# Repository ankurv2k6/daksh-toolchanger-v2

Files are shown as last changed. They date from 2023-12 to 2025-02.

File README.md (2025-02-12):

# DAKSH V2 3D Printed Tool Changer - Open Beta

DAKSH V2 3D Printed Tool Changer is a fully 3D printed mechanical tool changer compatible with different CoreXY platforms like the Voron Trident, 1.8, 2.4  and RatRig VCore 3. The servo less mechanical locking mechanism is inspired by the Prusa XL - but is fully 3d printed with metal inserts in the critical areas for rigidity and reliability.

Salient Features: 

  * Fully Mechanical Tool Changer
  * Ultra Fast tool changing time of under 4 seconds
  * Fully 3d Printed and assembled using off the shelf components - no machined parts required
  * Intelligent Error State Detection and Recovery minimizing failed prints
  * Intelligent Tool Heating Management for faster and efficient prints
  * Automatic XYZ calibration across the different tools
  * Capable of High accelerations and print speeds
  * Minimal loss in build space with the tool changer addition
  * Integrated nozzle ooze blockers for clean prints with minimal waste
  * Status LEDs on each toolhead for accurate visual state diagnosis
  * Custom Klipper configuration, modules and macros for an integrated software package
  * Stiff Wire Looms and recoil management - wire looms are entirely contained within the printer frame itself.
  * Fully Enclosed Design in the same design ethos as the original Voron Trident design - giving it the ability to print high temp materials like ABS, PA6-CF and PC-CF etc which require enclosed chambers.

The design is open source and can be used freely for non commercial purposes. 

Do join the discord group at the link below and subscribe to the Youtube channel for more updates and interesting projects like this.

* [Github](https://github.com/ankurv2k6/wp-daksh-toolchanger-v2)
* [Youtube](https://www.youtube.com/channel/UCr8K1tva2CaEhyqNyaEjq_w)
* [Daksh V2 Discord](https://discord.gg/wJqUzYxYXH)
* [BOM](https://github.com/ankurv2k6/daksh-toolchanger-v2/tree/main/BOM) Create a copy of this [Google sheet](https://docs.google.com/spreadsheets/d/11UvXF6FBCVRHxjejWgnOjJhMhHBDZpzY7ktGSjUUAWM/edit?usp=sharing) for a checklist

Build Log and Demo videos 
* COMING SOON....

**5 Colour PLA Print - 0.6mm Nozzle / 0.25 Layer Height / 23 Hours / 2000 Tool Changes - TimeLapse**
Vase Print (https://www.youtube.com/watch?v=5WeLoIn3UTw)
  
**5 Colour PLA Print - 0.6mm Nozzle / 0.25 Layer Height / 23 Hours / 2000 Tool Changes**
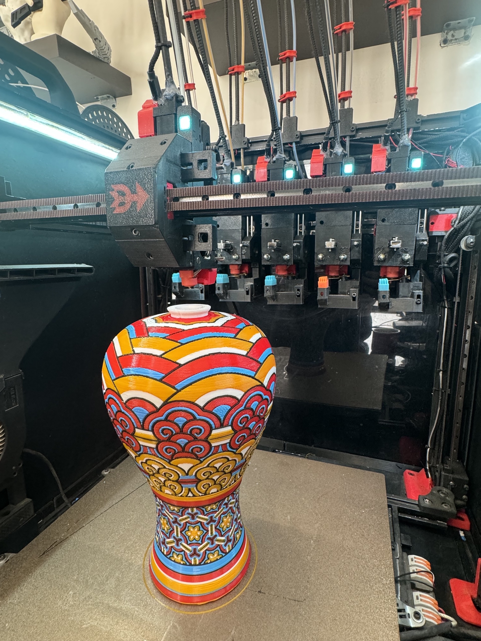
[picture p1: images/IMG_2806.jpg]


**5 Colour PLA Print - 0.6mm Nozzle / 0.25 Layer Height / 3 Hours / 300 Tool Changes**  
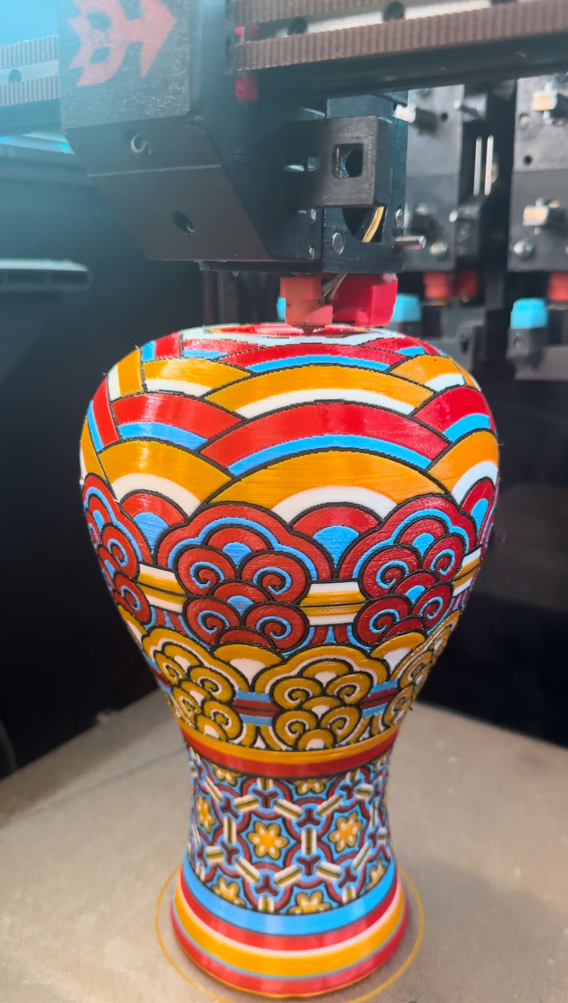
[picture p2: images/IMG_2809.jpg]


**TPU + PLA Print - 0.6mm Nozzle / 0.25 Layer Height / 23 Hours / 2000 Tool Changes**  
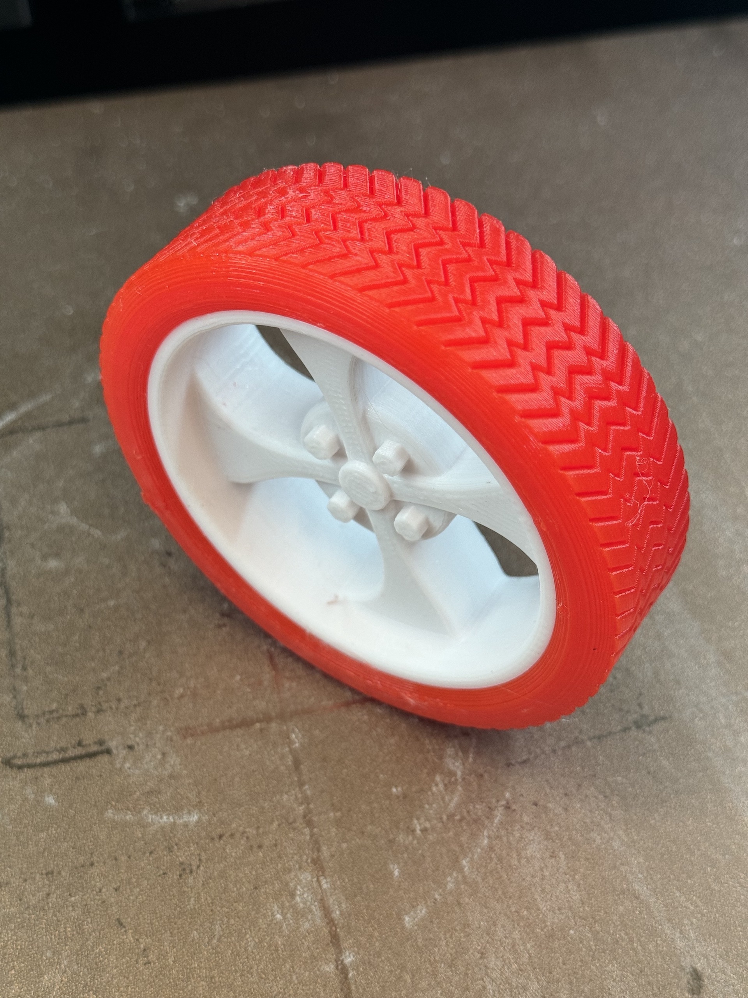
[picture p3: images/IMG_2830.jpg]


**TPU + PLA Print - 0.6mm Nozzle / 0.25 Layer Height / 8 Hours / 900 Tool Changes**  
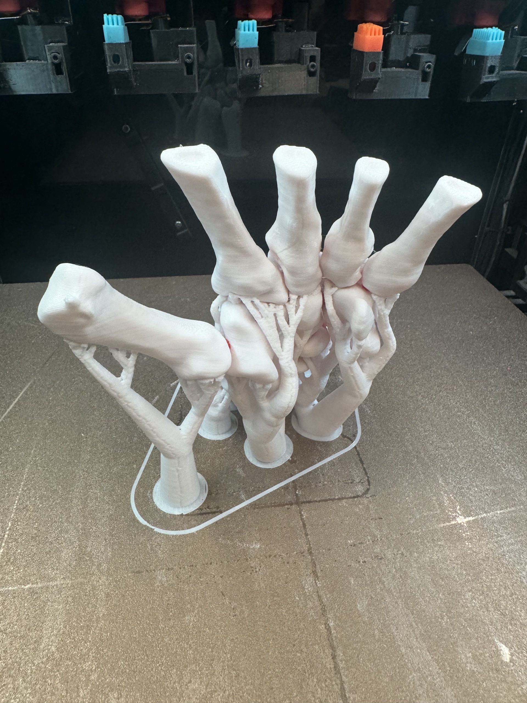
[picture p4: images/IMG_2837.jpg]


**5 Colour PLA + PETG Support print - 0.6mm Nozzle / 0.25 Layer Height / 3 Hours / 600 Tool Changes**  
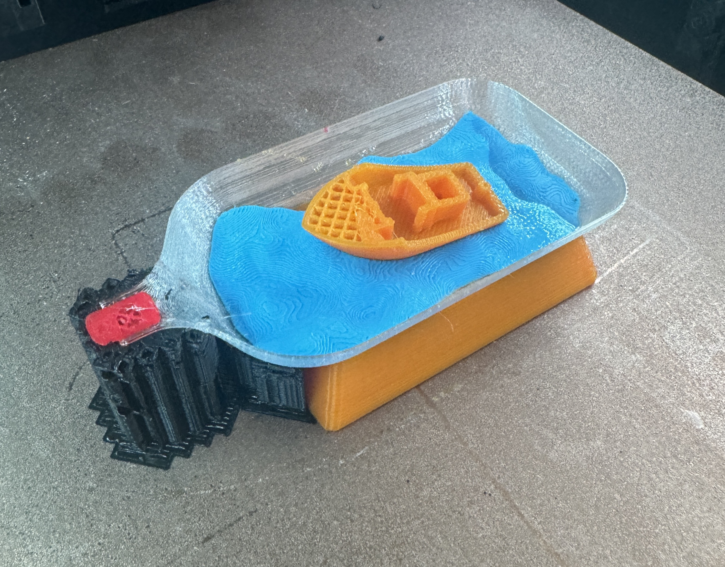
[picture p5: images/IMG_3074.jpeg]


Build Images
* COMING SOON....

Attributions - This project uses elements from a bunch of different projects by awesome people out there - I will be including a list of credits soon. My apologies for not doing that at the very onset due to paucity of time.

* [Quad Belted Z in based on the excellent work by genevamotion & thiagolocatelli](https://github.com/3DPrintingMods/VoronTrident-BeltedZ)

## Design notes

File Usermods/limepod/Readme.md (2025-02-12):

## limepod's mods

This is an overhaul of many parts, and none are made to be compatible with the original files.

* The XY Joints are modified to re-use the CNC top half from siboor
* The front idlers are remade to include tensioning, and moved forward to leave more space for the Y axis
* The A/B motor mounts are remade to be much bulkier, and the dock bar is now supported by aluminum brackets
* The carriage is modified to print in multiple parts, and various other changes to ease maintenance
* The toolheads have a number of changes, including the acorn nuts being shifted slightly, which makes them incompatible with the stock carriage

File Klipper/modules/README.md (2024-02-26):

Attributions

* Klipper Toolchanger - https://github.com/TypQxQ/Klipper_ToolChanger
* Tool Probe & Rounded Path - https://github.com/viesturz/klipper-toolchanger/
* Nozzle Align - https://github.com/viesturz/NozzleAlign
* ATC Switch - https://github.com/ben5459/Klipper_ToolChanger
* LED Effects - https://github.com/julianschill/klipper-led_effect

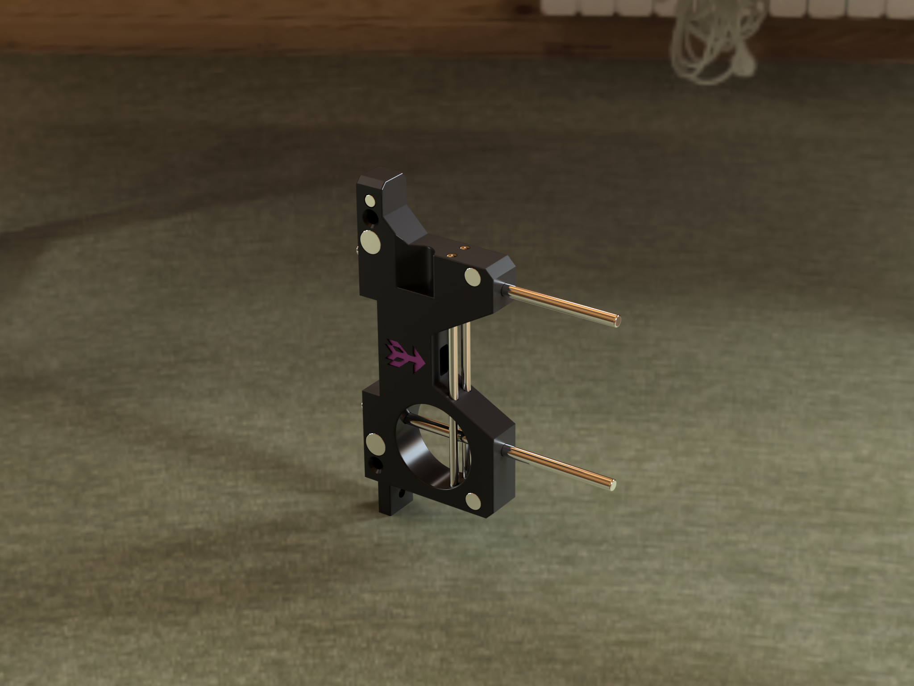
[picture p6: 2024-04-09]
Usermods/3dfiyMyLife/Sherpa-Mini-Orbiter-Extruder/Daksh Dock Mod.png

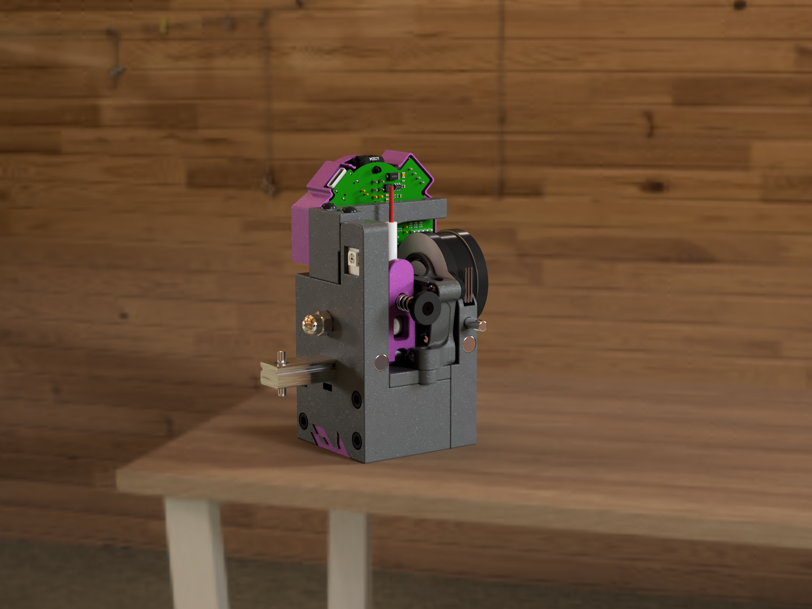
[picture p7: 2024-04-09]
Usermods/3dfiyMyLife/Sherpa-Mini-Orbiter-Extruder/Daksh Sherpa Mini.png

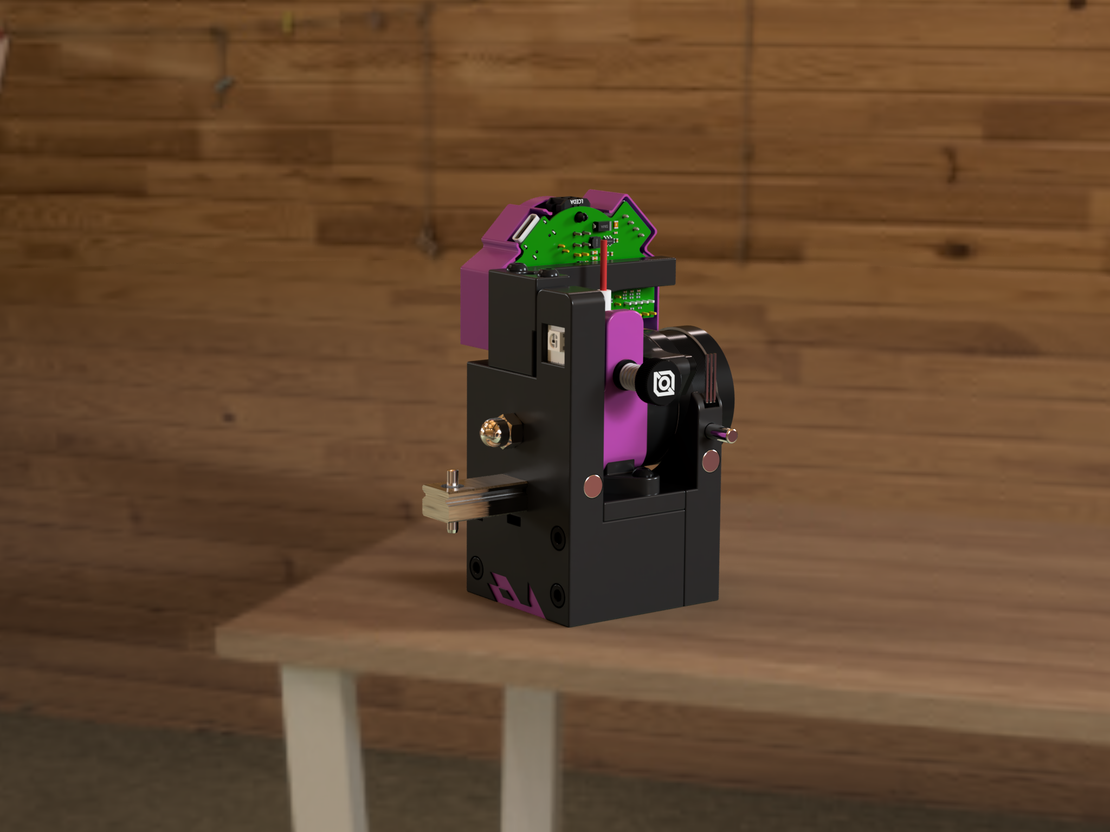
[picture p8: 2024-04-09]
Usermods/3dfiyMyLife/Sherpa-Mini-Orbiter-Extruder/Daksh Orbiter.png

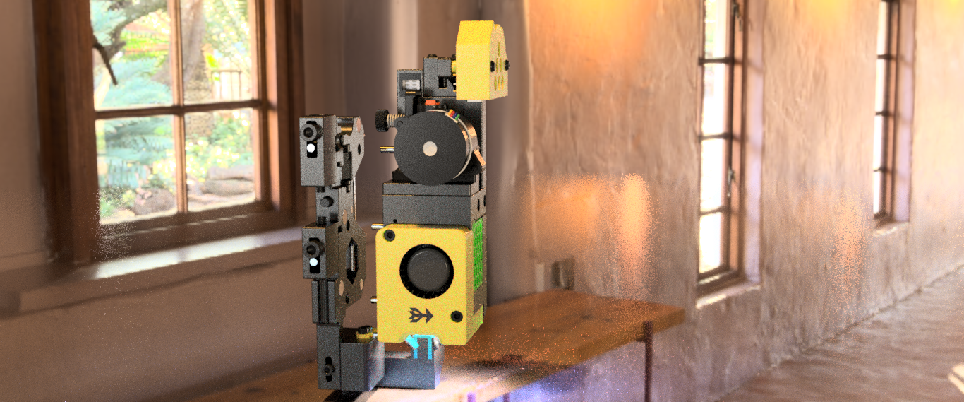
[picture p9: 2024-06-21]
CAD/V2ool/Rear_Docking/Daksh V2ool.png

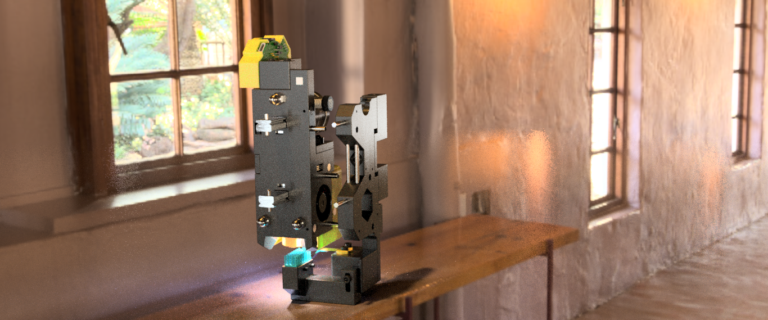
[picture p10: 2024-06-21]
CAD/V2ool/Rear_Docking/Daksh V2ool (1).png

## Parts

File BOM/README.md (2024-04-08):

Please refer to the [Google Sheets](https://docs.google.com/spreadsheets/d/11UvXF6FBCVRHxjejWgnOjJhMhHBDZpzY7ktGSjUUAWM/edit?usp=sharing) for the latest list

Create a copy of [Google Sheets](https://docs.google.com/spreadsheets/d/11UvXF6FBCVRHxjejWgnOjJhMhHBDZpzY7ktGSjUUAWM/edit?usp=sharing) to act as your own checklist 

| Item | Quantity |
|:---:|:---:|
| UM Bed Spring 6MM OD / 5MM ID | 8 |
| M3 x 16 Dowel Pins | 6 |
| M3 X 20 Dowel Pins | 6 |
| M3 x 30 Dowel Pins | 4 |
| M3 x16 Socket Head bolt | 2 |
| M3 x 20 Socket Head Bolt | 5 |
| M3 Hex Nut | 3 |
| M3 Square Nut - 2mm thick | 4 |
| M3 x 8 SHCS | 5 |
| 4mm x 4mm N52 Magnet | 1 |
| M3 Heat Set Inserts Voron Style | 9 |
| M3 Hex Nut | 3 |
| M3 Square Nut - thin | 2 |
| M3 x 12mm SHCS | 3 |
| M3 x 40mm SHCS | 1 |
| M3 x 16mm SHCS | 3 |
| M3 x 25mm SHCS | 4 |
| M3 x 30mm SHCS | 1 |
| M3 x 12 Flat Headed | 2 |
| M3 x 8 BHCS | 3 |
| M3 x 6mm SHCS | 2 |
| Nema 14 LDO Round Motor 10 teeth | 1 |
| Triangle Lab TD6S Hotend 24V | 1 |
| 3010 Axial Fan 24V | 1 |
| 4020 Blower Fan 24V | 1 |
| BMG Dual Extruder Gear set | 1 |
| EBB 36 Toolhead Board | 1 |
| Optical Endstop Switch | 1 |
| Neopixel LED | 1 |
| MGN12 Rails 35mm - Cut as per provided guide  | 2 |
| LM5UU Bearing | 1 |
| PC4-01 Pneumatic connector | 1 |
| M3 x10mm Spacers | 3 |
| 6mm x 3mm N52 Magnets | 3 |
| M5x24mm Dowel Pin / M5x25mm Dowel Pin | 1 |
| M3x20 Dowel Pin | 2 |
| MR63ZZ Bearing | 2 |
| M3x16 Dowel Pin | 2 |
| 6mm x 6mm N52 magnet | 1 |
| Hall Effect Sensor - AH3364Q | 2 |
| M4 x16mm Dowel Pin | 2 |
| M2.5 x 12 Socket Heads (For hotend mounting)  | 4 |
| PTFE Tube | 1 |
| 5mm - 6mm OD Spring - 4mm length - 0.5mm wire | 1 |
| M5 Acorn Nut | 3 |
| M5 x 6mm Heatset Inserts (Voron Knurled Type) | 3 |
| M5x12mm Set Screws | 3 |
| Superglue | |
| Loctite Thread Locker | |
| Glue Gun (for umbilical positioning) | |
| M4 x 30 SHCS | 2 |
| 6mmx3mm N52 magnets | 2 |
| 4mm x 4mm N52 magnets | 1 |
| 8mm x 5mm N52 magnets | 2 |
| M4 x 8mm Heatset Inserts | 2 |
| M4 Washer | 2 |
| M3 x 75mm Steel Rod | 2 |
| M4 x 95mm Steel Rod | 2 |
| 0.3mm -0.45mm Feeler Gauge Strip | 1 |
| M3 Washer | 1 |
| M3 T Nut Hammer Head Drop in | 1 |
| M5 x10 BHCS | 2 |
| M5 T Nut Hammer Head Drop in | 2 |

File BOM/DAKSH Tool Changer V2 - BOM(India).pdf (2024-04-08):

Ordered Arrived Item | Quantity | Price | URL/Link | Notes M4 x 30 SHCS | 2 | 3.07 https://omrook.com/fasteners/allen-bolts/shcs-allen/ss-allen-bolt-m4-x-30mm-dia.-4mm-length-30mm-stainless-steel-ss202-socket-head-cap-screws/
6mmx3mm N52 magnets | 2 | 20 https://www.patelmagnets.com/shop/6-x-3mm-neodymium-magnets/
4mm x 4mm N52 magnets | 1 | 10.9 https://www.patelmagnets.com/shop/4-x-4mm-neodymium-magnet/
8mm x 5mm N52 magnets | 2 | 33 https://www.patelmagnets.com/shop/8-x-5mm-neodymium-magnet/ M4 x 8mm Heatset Inserts | 2 | 50 https://robu.in/product/m4-x-8-mm-brass-heat-set-threaded-round-insert-nut-25-pcs/ Not ideal inserts. Try to use knurled like this: https://amzn.in/d/4WZXAzH M4 Washer | 2 | 0.59 https://omrook.com/fasteners/washer/flate-washer/m4-washer-dia-4mm-100-pcs/ M3 x 75mm Steel Rod | 2 | 100 https://robocraze.com/products/300mm-stainless-steel-rod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 One Rod is 300mm, you will need to cut it to size M4 x 95mm Steel Rod | 2 | 124 https://roboticsdna.in/product/4mm-dia-115mm-long-chrome-plated-smooth-rod One Rod is 115mm, you will need to cut it to size
0.3mm -0.45mm Feeler Gauge Strip | 1 | 369 | https://amzn.in/d/dUbM6hw It is a whole set of feeler guages, you can find cheaper individual one locally Full set of feeler gauges M3 x 25mm SHCS | 1 | 2.83 | https://omrook.com/fasteners/allen-bolts/shcs-allen/ss-allen-bolt-m4-x-25mm-dia.-4mm-length-25mm-stainless-steel-ss202-socket-head-cap-screws/ M3 Washer | 1 | 0.59 | https://omrook.com/fasteners/washer/flate-washer/m3-washer-zink-white-dia-3mm-100-pcs/ M3 T Nut Hammer Head Drop in | 1 | 6.9 | https://novo3d.in/hammernut/ M5 x10 BHCS | 2 | 2.36 | https://omrook.com/fasteners/allen-bolts/shcs-allen/ss-allen-bolt-m5-x-10mm-dia.-5mm-length-10mm-stainless-steel-ss202-socket-head-cap-screws/ M5 T Nut Hammer Head Drop in | 2 | 6.9 | https://novo3d.in/hammernut/
Silicone Nozzle Cleaner | 1 | 53 | https://amzn.in/d/6Rx3F1c
Total Price | Rs. | 1123.06

Ordered Arrived | Item | Quantity | Price | URL/Link
UM Bed Spring 6MM OD / 5MM ID | 8 | 90.86 | Heat Bed Spacer Spring for 3D Printer UM2 Ultimaker2 (4Pcs) – RoboticsDNA (https://roboticsdna.in/product/heat-bed-spacer-spring-for-3d-printer-um2-ultimaker2-4pcs/) M3 x 16 Dowel Pins | 6 | 19 | https://thinkrobotics.com/products/stainless-steel-dowel-pins-assembly-pins-pack-of-10?variant=39636812300374 M3 X 20 Dowel Pins | 6 | 19 | https://thinkrobotics.com/products/stainless-steel-dowel-pins-assembly-pins-pack-of-10?variant=39636812333142 M3 x 30 Dowel Pins | 4 | 22.9 | https://thinkrobotics.com/products/stainless-steel-dowel-pins-assembly-pins-pack-of-10?variant=39636812398678 M3 x16 Socket Head bolt | 2 | 1.42 | SS Allen Bolt M3 x 16mm, Dia. 3mm, Length 16mm, Stainless Steel (SS202) Socket Head Cap Screws from India Local Shop and Omrook M3 x 20 Socket Head Bolt | 5 | 2.6 | SS Allen Bolt M3 x 20mm, Dia. 3mm, Length 20mm, Stainless Steel (SS202) Socket Head Cap Screws M3 Hex Nut | 3 | 0.59 | M3 (3mm) Hex Nut White from India Local Shop and Omrook M3 Square Nut - 2mm thick | 4 | 0.83 | M3 Square Nut from India Local Shop and Omrook M3 x 8 Socket head Bolt | 4 | 1.65 | SS Allen Bolt M3 x 8mm, Dia. 3mm, Length 8mm, Stainless Steel (SS202) Socket Head Cap Screws
4mm x 4mm N52 Magnet | 1 | 10.9 | https://www.patelmagnets.com/shop/4-x-4mm-neodymium-magnet/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
Total Price | Rs. | 1084.91

Ordered Arrived | Item | Quantity | Price | URL/Link | Notes
Fasteners M3 Heat Set Inserts Voron Style | 9 | 7 https://dc3d.in/shop/hardwares/m3-heat-set-insert/ M3 Hex Nut | 3 | 0.59 https://omrook.com/fasteners/nut/hex-nut/m3-3mm-hex-nut-white/ M3 Square Nut - thin | 2 | 0.83 https://omrook.com/fasteners/nut/square-nut/m3-square-nut-100-pcs/
M3 x 12mm SHCS | 3 | 1.65

https://omrook.com/fasteners/allen-bolts/shcs-allen/ss-allen-bolt-m3-x-12mm-dia.-3mm-length-12mm-stainless- steel-ss202-socket-head-cap-screws/

M3 x 40mm SHCS | 1 | 5.9

https://omrook.com/fasteners/allen-bolts/shcs-allen/ss-allen-bolt-m3-x-40mm-dia.-3mm-length-40mm-stainless- steel-ss202-socket-head-cap-screws/

M3 x 8mm SHCS | 1 | 1.65

https://omrook.com/fasteners/allen-bolts/shcs-allen/ss-allen-bolt-m3-x-8mm-dia.-3mm-length-8mm-stainless-steel- ss202-socket-head-cap-screws/

M3 x 16mm SHCS | 3 | 1.42

https://omrook.com/fasteners/allen-bolts/shcs-allen/ss-allen-bolt-m3-x-16mm-dia.-3mm-length-16mm-stainless- steel-ss202-socket-head-cap-screws/

M3 x 25mm SHCS | 3 | 2.95

https://omrook.com/fasteners/allen-bolts/shcs-allen/ss-allen-bolt-m3-x-25mm-dia.-3mm-length-25mm-stainless- steel-ss202-socket-head-cap-screws/

M3 x 30mm SHCS | 1 | 3.3

https://omrook.com/fasteners/allen-bolts/shcs-allen/ss-allen-bolt-m3-x-30mm-dia.-3mm-length-30mm-stainless- steel-ss202-socket-head-cap-screws/

M3 x 12 Flat Headed | 2 | 70

https://robu.in/product/easymech-ss-304-csk-countersunk-philips-head-m3-x-12-mm-bolt-25-pcs/?
gad_source=1&gclid=CjwKCAjw_LOwBhBFEiwAmSEQARgZ3eb62c4tams- (https://robu.in/product/easymech-ss-304-csk-countersunk-philips-head-m3-x-12-mm-bolt-25-pcs/?gad_source=1) DFXlXLo3CkbqY45yWWkLrs6E920c_8iq71QwvhoCOqYQAvD_BwE | Set of 25
M3 x 8 BHCS | 3 | 0.83

https://omrook.com/fasteners/allen-bolts/button-allen/ss-button-allen-m3-x-8mm-dia.-3mm-length-8mm-stainless- steel-ss202-allen-socket-button-screws/

M3 x 6mm SHCS | 2 | 0.71

https://omrook.com/fasteners/allen-bolts/button-allen/ss-button-allen-m3-x-6mm-dia.-3mm-length-6mm-stainless- steel-ss202-allen-socket-button-screws/

Extruder & Electronics Nema 14 LDO Round Motor 10 teeth | 1 | 799 https://novo3d.in/nema14-stepper-motor/
Triangle Lab TD6S Hotend 24V | 1 | 2299 https://novo3d.in/bambu-lab/?swcfpc=1 | (Just a place holder, look at international for proper part)Any hotend with Dragon style top mounting holes will work with mods to the parts cooling fan for nozzle alignment
3010 Axial Fan 24V | 1 | 75

https://robu.in/product/dc-24v-3010-hydraulic-cooling-fan-with-xh2-54-2p-30cm-cable-size303010mm/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 (https://robu.in/product/dc-24v-3010-hydraulic-cooling-fan-with-xh2-54-2p-30cm-cable-size303010mm/?gad_source=1) sBhBSEiwAWWzTnlZM0cRrKdnI_cvYdec7NqjQucmIkH4QZt1_jco9j0gfAHAFARGBdRoCG4wQAvD_BwE

4020 Blower Fan 24V | 1 | 208

https://robu.in/product/dc-24v-4020-hydraulic-centrifugal-fan-with-xh2-54-2p-30cm-cable-size404020mm/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 (https://robu.in/product/dc-24v-4020-hydraulic-centrifugal-fan-with-xh2-54-2p-30cm-cable-size404020mm/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) sBhBSEiwAWWzTnsH9nyb0sDOZvDX9zfyAz4EfAAffYyIyJKioHY3RkaaNkblqMviBhhoCcugQAvD_BwE

BMG Dual Extruder Gear set | 1 | 399 https://novo3d.in/bmg-gear/?swcfpc=1 EBB 36 Toolhead Board | 1 | 1779 https://novo3d.in/bigtreetech-ebb36-canbus/?swcfpc=1 Optical Endstop Switch | 1 | 54 https://robu.in/product/optical-endstop-light-control-limit-optical-switch/
Neopixel LED | 1 | 212

https://robu.in/product/ws2812b-rgb-addressable-led-module/?gad_source=1&gclid=CjwKCAiAyp- sBhBSEiwAWWzTnjCfczEAywwFA0H_ZiDocRcNEUFVyRXAswYWu_UGx7z-FyoMltsvABoCAS4QAvD_BwE

1 Hardware MGN12 Rails 35mm - Cut as per provided guide | 2 | 2699 | https://novo3d.in/mgn12h-linear-rail/ can find used rails for a lot cheaper | 100mm Rail per tool is required to obtain 2x35mm cuts
LM5UU Bearing | 1 | 89 | https://www.flyrobo.in/lm5uu-5mm-linear-motion-bearing-for-3d-printer PC4-01 Pneumatic connector | 1 | 27 | https://robu.in/product/pc4-01-pneumatic-push-for-v6-bowden-extruders-4mm-tube-j-head-fitting M3 x10mm Spacers | 3 | 100 | https://thinkrobotics.com/products/aluminium-spacers-pack-of-10?variant=39715551314006
6mm x 3mm N52 Magnets | 3 | 20 | https://www.patelmagnets.com/shop/6-x-3mm-neodymium-magnets M5x24mm Dowel Pin / M5x25mm Dowel Pin | 1 | 85 | https://www.3dprintronics.com/products/M5-Dowel-Pin-Straight-Type-MISUMI-p545184955 M3x20 Dowel Pin | 2 | 85 | https://www.3dprintronics.com/products/M3-Dowel-Pin-Straight-Type-MISUMI-p551575791 MR63ZZ Bearing | 2 | 870 | https://amzn.in/d/e7LxKSf Price is For moq Actuall price for qty is only Rs.174 | (Place Holder) M3x16 Dowel Pin | 2 | 75 | https://robocraze.com/products/16mm-alloy-steel-dowel-pins-pack-of-10
6mm x 6mm N52 magnet | 1 | 28 | https://www.patelmagnets.com/shop/6-x-6mm-neodymium-magnets/?attribute_pa_grade=n52 Hall Effect Sensor - AH3364Q | 2 M4 x16mm Dowel Pin | 2 | 200 | https://thinkrobotics.com/products/stainless-steel-dowel-pins-assembly-pins-pack-of-10?variant=39636812496982 M2.5 x 12 Socket Heads (For hotend mounting) | 4 | 20 | https://www.fastdep.in/product/pan-head-screw-m2-5x12mm/ | place holder) PTFE Tube | 1 | Cut to length based on hotend - decrease measured length by 3mm to allow for z probe movement
5mm - 6mm OD Spring - 4mm length - 0.5mm wire | 1 | 90.86 | Heat Bed Spacer Spring for 3D Printer UM2 Ultimaker2 (4Pcs) – RoboticsDNA (https://roboticsdna.in/product/heat-bed-spacer-spring-for-3d-printer-um2-ultimaker2-4pcs/) | Cut from larger spring - 4 loops
KInematic Coupling M5 Acorn Nut | 3 | 30 | https://robu.in/product/easymech-m5-ms-dome-nut-acorn-nut-25-pcs/? M5 x 6mm Heatset Inserts (Voron Knurled Type) | 3 | https://www.partsbuilt.com/m5-heat-set-thread-insert-6mm-long-4-pack/ M5x12mm Set Screws | 3 | 10 | https://robu.in/product/easymech-m5-x-12mm-socket-set-screws-allen-grub-10pcs/

Superglue
Loctite Thread Locker Glue Gun (for umbilical positioning)
Total Price | Rs. | 14802.11

Ordered | Arrived | Item | Quantity | Price | URL/Link M4 x 30 SHCS | 2 | 3.07 | https://omrook.com/fasteners/allen-bolts/shcs-allen/ss-allen-bolt-m4-x-30mm-dia.-4mm-length-30mm-stainless-steel-ss202-socket-head-cap-screws/
6mmx3mm N52 magnets | 2 | 20 | https://www.patelmagnets.com/shop/6-x-3mm-neodymium-magnets/
4mm x 4mm N52 magnets | 1 | 10.9 | https://www.patelmagnets.com/shop/4-x-4mm-neodymium-magnet/
8mm x 5mm N52 magnets | 2 | 33 | https://www.patelmagnets.com/shop/8-x-5mm-neodymium-magnet/ M4 x 8mm Heatset Inserts | 2 | 50 | https://robu.in/product/m4-x-8-mm-brass-heat-set-threaded-round-insert-nut-25-pcs/ Not ideal inserts. Try to use knurled like this: https://amzn.in/d/4WZXAzH M4 Washer | 2 | 0.59 | https://omrook.com/fasteners/washer/flate-washer/m4-washer-dia-4mm-100-pcs/ M3 x 75mm Steel Rod | 2 | 100 | https://robocraze.com/products/300mm-stainless-steel-rod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 One Rod is 300mm, you will need to cut it to size M4 x 95mm Steel Rod | 2 | 124 | https://roboticsdna.in/product/4mm-dia-115mm-long-chrome-plated-smooth-rodOne Rod is 115mm, you will need to cut it to size
0.3mm -0.45mm Feeler Gauge Strip | 1 | 369 | https://amzn.in/d/dUbM6hw It is a whole set of feeler guages, you can find cheaper individual one locally Full set of feeler gauges M3 x 25mm SHCS | 1 | 2.83 | https://omrook.com/fasteners/allen-bolts/shcs-allen/ss-allen-bolt-m4-x-25mm-dia.-4mm-length-25mm-stainless-steel-ss202-socket-head-cap-screws/ M3 Washer | 1 | 0.59 | https://omrook.com/fasteners/washer/flate-washer/m3-washer-zink-white-dia-3mm-100-pcs/ M3 T Nut Hammer Head Drop in | 1 | 6.9 | https://novo3d.in/hammernut/ M5 x10 BHCS | 2 | 2.36 | https://omrook.com/fasteners/allen-bolts/shcs-allen/ss-allen-bolt-m5-x-10mm-dia.-5mm-length-10mm-stainless-steel-ss202-socket-head-cap-screws/ M5 T Nut Hammer Head Drop in | 2 | 6.9 | https://novo3d.in/hammernut/
Silicone Nozzle Cleaner | 1 | 53 | https://amzn.in/d/6Rx3F1c UM Bed Spring 6MM OD / 5MM ID | 8 | 90.86 | Heat Bed Spacer Spring for 3D Printer UM2 Ultimaker2 (4Pcs) – RoboticsDNA M3 x 16 Dowel Pins | 6 | 19 | https://thinkrobotics.com/products/stainless-steel-dowel-pins-assembly-pins-pack-of-10?variant=39636812300374 M3 X 20 Dowel Pins | 6 | 19 | https://thinkrobotics.com/products/stainless-steel-dowel-pins-assembly-pins-pack-of-10?variant=39636812333142 M3 x 30 Dowel Pins | 4 | 22.9 | https://thinkrobotics.com/products/stainless-steel-dowel-pins-assembly-pins-pack-of-10?variant=39636812398678 M3 x16 Socket Head bolt | 2 | 1.42 | SS Allen Bolt M3 x 16mm, Dia. 3mm, Length 16mm, Stainless Steel (SS202) Socket Head Cap Screws from India Local Shop and Omrook M3 x 20 Socket Head Bolt | 5 | 2.6 | SS Allen Bolt M3 x 20mm, Dia. 3mm, Length 20mm, Stainless Steel (SS202) Socket Head Cap Screws M3 Hex Nut | 3 | 0.59 | M3 (3mm) Hex Nut White from India Local Shop and Omrook M3 Square Nut - 2mm thick | 4 | 0.83 | M3 Square Nut from India Local Shop and Omrook M3 x 8 Socket head Bolt | 4 | 1.65 | SS Allen Bolt M3 x 8mm, Dia. 3mm, Length 8mm, Stainless Steel (SS202) Socket Head Cap Screws
4mm x 4mm N52 Magnet | 1 | 10.9 | https://www.patelmagnets.com/shop/4-x-4mm-neodymium-magnet/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
Fasteners M3 Heat Set Inserts Voron Style | 9 | 7 | https://dc3d.in/shop/hardwares/m3-heat-set-insert/ M3 Hex Nut | 3 | 0.59 | https://omrook.com/fasteners/nut/hex-nut/m3-3mm-hex-nut-white/ M3 Square Nut - thin | 2 | 0.83 | https://omrook.com/fasteners/nut/square-nut/m3-square-nut-100-pcs/
M3 x 12mm SHCS | 3 | 1.65

https://omrook.com/fasteners/allen-bolts/shcs-allen/ss-allen-bolt-m3-x- 12mm-dia.-3mm-length-12mm-stainless-steel-ss202-socket-head-cap-

screws/ (https://omrook.com/fasteners/allen-bolts/shcs-allen/ss-allen-bolt-m3-x-12mm-dia.-3mm-length-12mm-stainless-steel-ss202-socket-head-cap-screws/)

M3 x 40mm SHCS | 1 | 5.9

https://omrook.com/fasteners/allen-bolts/shcs-allen/ss-allen-bolt-m3-x- 40mm-dia.-3mm-length-40mm-stainless-steel-ss202-socket-head-cap-

screws/ (https://omrook.com/fasteners/allen-bolts/shcs-allen/ss-allen-bolt-m3-x-40mm-dia.-3mm-length-40mm-stainless-steel-ss202-socket-head-cap-screws/)

M3 x 8mm SHCS | 1 | 1.65

https://omrook.com/fasteners/allen-bolts/shcs-allen/ss-allen-bolt-m3-x- 8mm-dia.-3mm-length-8mm-stainless-steel-ss202-socket-head-cap-screws/

M3 x 16mm SHCS | 3 | 1.42

https://omrook.com/fasteners/allen-bolts/shcs-allen/ss-allen-bolt-m3-x- 16mm-dia.-3mm-length-16mm-stainless-steel-ss202-socket-head-cap-

screws/ (https://omrook.com/fasteners/allen-bolts/shcs-allen/ss-allen-bolt-m3-x-16mm-dia.-3mm-length-16mm-stainless-steel-ss202-socket-head-cap-screws/)

M3 x 25mm SHCS | 3 | 2.95

https://omrook.com/fasteners/allen-bolts/shcs-allen/ss-allen-bolt-m3-x- 25mm-dia.-3mm-length-25mm-stainless-steel-ss202-socket-head-cap-

screws/ (https://omrook.com/fasteners/allen-bolts/shcs-allen/ss-allen-bolt-m3-x-25mm-dia.-3mm-length-25mm-stainless-steel-ss202-socket-head-cap-screws/)

M3 x 30mm SHCS | 1 | 3.3

https://omrook.com/fasteners/allen-bolts/shcs-allen/ss-allen-bolt-m3-x- 30mm-dia.-3mm-length-30mm-stainless-steel-ss202-socket-head-cap-

screws/ (https://omrook.com/fasteners/allen-bolts/shcs-allen/ss-allen-bolt-m3-x-30mm-dia.-3mm-length-30mm-stainless-steel-ss202-socket-head-cap-screws/)

M3 x 12 Flat Headed | 2 | 70

https://robu.in/product/easymech-ss-304-csk-countersunk-philips-head-m3-x-12-mm-bolt-25-pcs/?
gad_source=1&gclid=CjwKCAjw_LOwBhBFEiwAmSEQARgZ3eb62c4tams- (https://robu.in/product/easymech-ss-304-csk-countersunk-philips-head-m3-x-12-mm-bolt-25-pcs/?gad_source=1) DFXlXLo3CkbqY45yWWkLrs6E920c_8iq71QwvhoCOqYQAvD_BwE | Set of 25
M3 x 8 BHCS | 3 | 0.83

https://omrook.com/fasteners/allen-bolts/button-allen/ss-button-allen-m3-x- 8mm-dia.-3mm-length-8mm-stainless-steel-ss202-allen-socket-button-

screws/ (https://omrook.com/fasteners/allen-bolts/button-allen/ss-button-allen-m3-x-8mm-dia.-3mm-length-8mm-stainless-steel-ss202-allen-socket-button-screws/)
M3 x 6mm SHCS | 2 | 0.71 | https://omrook.com/fasteners/allen-bolts/button-allen/ss-button-allen-m3-x- 6mm-dia.-3mm-length-6mm-stainless-steel-ss202-allen-socket-button- screws/ (https://omrook.com/fasteners/allen-bolts/button-allen/ss-button-allen-m3-x-6mm-dia.-3mm-length-6mm-stainless-steel-ss202-allen-socket-button-screws/)
Extruder & Electronics Nema 14 LDO Round Motor 10 teeth | 1 | 799 | https://novo3d.in/nema14-stepper-motor/
Triangle Lab TD6S Hotend 24V | 1 | 2299 | https://novo3d.in/bambu-lab/?swcfpc=1 | (Just a place holder, look at international for proper part)Any hotend with Dragon style top mounting holes will work with mods to the parts cooling fan for nozzle alignment
3010 Axial Fan 24V | 1 | 75

https://robu.in/product/dc-24v-3010-hydraulic-cooling-fan-with-xh2-54-2p- 30cm-cable-size303010mm/?gad_source=1&gclid=CjwKCAiAyp-

sBhBSEiwAWWzTnlZM0cRrKdnI_cvYdec7NqjQucmIkH4QZt1_jco9j0gfAH AFARGBdRoCG4wQAvD_BwE (https://robu.in/product/dc-24v-3010-hydraulic-cooling-fan-with-xh2-54-2p-30cm-cable-size303010mm/?gad_source=1)

4020 Blower Fan 24V | 1 | 208

https://robu.in/product/dc-24v-4020-hydraulic-centrifugal-fan-with-xh2-54- 2p-30cm-cable-size404020mm/?gad_source=1&gclid=CjwKCAiAyp-

sBhBSEiwAWWzTnsH9nyb0sDOZvDX9zfyAz4EfAAffYyIyJKioHY3RkaaNk (https://robu.in/product/dc-24v-4020-hydraulic-centrifugal-fan-with-xh2-54-2p-30cm-cable-size404020mm/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) blqMviBhhoCcugQAvD_BwE

BMG Dual Extruder Gear set | 1 | 399 | https://novo3d.in/bmg-gear/?swcfpc=1
EBB 36 Toolhead Board | 1 | 1779 | https://novo3d.in/bigtreetech-ebb36-canbus/?swcfpc=1 Optical Endstop Switch | 1 | 54 | https://robu.in/product/optical-endstop-light-control-limit-optical-switch/
Neopixel LED | 1 | 212

https://robu.in/product/ws2812b-rgb-addressable-led-module/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 (https://robu.in/product/ws2812b-rgb-addressable-led-module/?gad_source=1) 7z-FyoMltsvABoCAS4QAvD_BwE

1 Hardware MGN12 Rails 35mm - Cut as per provided guide | 2 | 2699 | https://novo3d.in/mgn12h-linear-rail/ can find used rails for a lot cheaper | 100mm Rail per tool is required to obtain 2x35mm cuts
LM5UU Bearing | 1 | 89 | https://www.flyrobo.in/lm5uu-5mm-linear-motion-bearing-for-3d-printer

PC4-01 Pneumatic connector | 1 | 27

https://robu.in/product/pc4-01-pneumatic-push-for-v6-bowden-extruders- 4mm-tube-j-head-fitting

M3 x10mm Spacers | 3 | 100 | https://thinkrobotics.com/products/aluminium-spacers-pack-of-10? variant=39715551314006 (https://thinkrobotics.com/products/aluminium-spacers-pack-of-10?variant=39715551314006)
6mm x 3mm N52 Magnets | 3 | 20 | https://www.patelmagnets.com/shop/6-x-3mm-neodymium-magnets
M5x24mm Dowel Pin / M5x25mm Dowel Pin | 1 | 85 | https://www.3dprintronics.com/products/M5-Dowel-Pin-Straight-Type- MISUMI-p545184955
M3x20 Dowel Pin | 2 | 85

https://www.3dprintronics.com/products/M3-Dowel-Pin-Straight-Type- MISUMI-p551575791

MR63ZZ Bearing | 2 | 870
https://amzn.in/d/e7LxKSf Price is For moq Actuall price for qty is only Rs. 174 | (Place Holder) M3x16 Dowel Pin | 2 | 75 | https://robocraze.com/products/16mm-alloy-steel-dowel-pins-pack-of-10
6mm x 6mm N52 magnet | 1 | 28

https://www.patelmagnets.com/shop/6-x-6mm-neodymium-magnets/?
attribute_pa_grade=n52 (https://www.patelmagnets.com/shop/6-x-6mm-neodymium-magnets/?attribute_pa_grade=n52) Hall Effect Sensor - AH3364Q | 2
M4 x16mm Dowel Pin | 2 | 200
https://thinkrobotics.com/products/stainless-steel-dowel-pins-assembly- pins-pack-of-10?variant=39636812496982 M2.5 x 12 Socket Heads (For hotend mounting) | 4 | 20 | https://www.fastdep.in/product/pan-head-screw-m2-5x12mm/ | place holder)
PTFE Tube | 1 | Cut to length based on hotend - decrease measured length by 3mm to allow for z probe movement
5mm - 6mm OD Spring - 4mm length - 0.5mm wire1 | 90.86 | Heat Bed Spacer Spring for 3D Printer UM2 Ultimaker2 (4Pcs) – RoboticsDNACut (https://roboticsdna.in/product/heat-bed-spacer-spring-for-3d-printer-um2-ultimaker2-4pcs/) from larger spring - 4 loops
KInematic Coupling M5 Acorn Nut | 3 | 30 | https://robu.in/product/easymech-m5-ms-dome-nut-acorn-nut-25-pcs/? M5 x 6mm Heatset Inserts (Voron Knurled Type) 3 | https://www.partsbuilt.com/m5-heat-set-thread-insert-6mm-long-4-pack/
M5x12mm Set Screws | 3 | 10

https://robu.in/product/easymech-m5-x-12mm-socket-set-screws-allen- grub-10pcs/

Superglue
Loctite Thread Locker Glue Gun (for umbilical positioning)
Total Price | Rs. 17010.08

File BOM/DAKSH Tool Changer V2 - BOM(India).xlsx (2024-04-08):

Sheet: Dock
Ordered | Arrived | Item | Quantity | Price | URL/Link | Notes
FALSE | FALSE | M4 x 30 SHCS | 2 | 3.07 | https://omrook.com/fasteners/allen-bolts/shcs-allen/ss-allen-bolt-m4-x-30mm-dia.-4mm-length-30mm-stainless-steel-ss202-socket-head-cap-screws/
FALSE | FALSE | 6mmx3mm N52 magnets | 2 | 20 | https://www.patelmagnets.com/shop/6-x-3mm-neodymium-magnets/
FALSE | FALSE | 4mm x 4mm N52 magnets | 1 | 10.9 | https://www.patelmagnets.com/shop/4-x-4mm-neodymium-magnet/
FALSE | FALSE | 8mm x 5mm N52 magnets | 2 | 33 | https://www.patelmagnets.com/shop/8-x-5mm-neodymium-magnet/
FALSE | FALSE | M4 x 8mm Heatset Inserts | 2 | 50 | https://robu.in/product/m4-x-8-mm-brass-heat-set-threaded-round-insert-nut-25-pcs/ | Not ideal inserts. Try to use knurled like this: https://amzn.in/d/4WZXAzH
FALSE | FALSE | M4 Washer | 2 | 0.59 | https://omrook.com/fasteners/washer/flate-washer/m4-washer-dia-4mm-100-pcs/
FALSE | FALSE | M3 x 75mm Steel Rod | 2 | 100 | https://robocraze.com/products/300mm-stainless-steel-rod?variant=40193979154585&currency=INR | One Rod is 300mm, you will need to cut it to size
FALSE | FALSE | M4 x 95mm Steel Rod | 2 | 124 | https://roboticsdna.in/product/4mm-dia-115mm-long-chrome-plated-smooth-rod | One Rod is 115mm, you will need to cut it to size
FALSE | FALSE | 0.3mm -0.45mm Feeler Gauge Strip | 1 | 369 | https://amzn.in/d/dUbM6hw It is a whole set of feeler guages, you can find cheaper individual one locally | Full set of feeler gauges
FALSE | FALSE | M3 x 25mm SHCS | 1 | 2.83 | https://omrook.com/fasteners/allen-bolts/shcs-allen/ss-allen-bolt-m4-x-25mm-dia.-4mm-length-25mm-stainless-steel-ss202-socket-head-cap-screws/
FALSE | FALSE | M3 Washer | 1 | 0.59 | https://omrook.com/fasteners/washer/flate-washer/m3-washer-zink-white-dia-3mm-100-pcs/
FALSE | FALSE | M3 T Nut Hammer Head Drop in | 1 | 6.9 | https://novo3d.in/hammernut/
FALSE | FALSE | M5 x10 BHCS | 2 | 2.36 | https://omrook.com/fasteners/allen-bolts/shcs-allen/ss-allen-bolt-m5-x-10mm-dia.-5mm-length-10mm-stainless-steel-ss202-socket-head-cap-screws/
FALSE | FALSE | M5 T Nut Hammer Head Drop in | 2 | 6.9 | https://novo3d.in/hammernut/
FALSE | FALSE | Silicone Nozzle Cleaner | 1 | 53 | https://amzn.in/d/6Rx3F1c
 |  | Total Price | Rs. | 1123.06

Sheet: Tool Lock Carriage
Ordered | Arrived | Item | Quantity | Price | URL/Link
FALSE | FALSE | UM Bed Spring 6MM OD / 5MM ID | 8 | 90.86 | Heat Bed Spacer Spring for 3D Printer UM2 Ultimaker2 (4Pcs) – RoboticsDNA (https://roboticsdna.in/product/heat-bed-spacer-spring-for-3d-printer-um2-ultimaker2-4pcs/)
FALSE | FALSE | M3 x 16 Dowel Pins | 6 | 19 | https://thinkrobotics.com/products/stainless-steel-dowel-pins-assembly-pins-pack-of-10?variant=39636812300374
FALSE | FALSE | M3 X 20 Dowel Pins | 6 | 19 | https://thinkrobotics.com/products/stainless-steel-dowel-pins-assembly-pins-pack-of-10?variant=39636812333142
FALSE | FALSE | M3 x 30 Dowel Pins | 4 | 22.9 | https://thinkrobotics.com/products/stainless-steel-dowel-pins-assembly-pins-pack-of-10?variant=39636812398678
FALSE | FALSE | M3 x16 Socket Head bolt | 2 | 1.42 | SS Allen Bolt M3 x 16mm, Dia. 3mm, Length 16mm, Stainless Steel (SS202) Socket Head Cap Screws from India Local Shop and Omrook (https://omrook.com/fasteners/allen-bolts/shcs-allen/ss-allen-bolt-m3-x-16mm-dia.-3mm-length-16mm-stainless-steel-ss202-socket-head-cap-screws/)
FALSE | FALSE | M3 x 20 Socket Head Bolt | 5 | 2.6 | SS Allen Bolt M3 x 20mm, Dia. 3mm, Length 20mm, Stainless Steel (SS202) Socket Head Cap Screws (https://omrook.com/fasteners/allen-bolts/shcs-allen/ss-allen-bolt-m3-x-20mm-dia.-3mm-length-20mm-stainless-steel-ss202-socket-head-cap-screws/)
FALSE | FALSE | M3 Hex Nut | 3 | 0.59 | M3 (3mm) Hex Nut White from India Local Shop and Omrook (https://omrook.com/fasteners/nut/hex-nut/m3-3mm-hex-nut-white/)
FALSE | FALSE | M3 Square Nut - 2mm thick | 4 | 0.83 | M3 Square Nut from India Local Shop and Omrook (https://omrook.com/fasteners/nut/square-nut/m3-square-nut-100-pcs/)
FALSE | FALSE | M3 x 8 Socket head Bolt | 4 | 1.65 | SS Allen Bolt M3 x 8mm, Dia. 3mm, Length 8mm, Stainless Steel (SS202) Socket Head Cap Screws (https://omrook.com/fasteners/allen-bolts/shcs-allen/ss-allen-bolt-m3-x-8mm-dia.-3mm-length-8mm-stainless-steel-ss202-socket-head-cap-screws/)
FALSE | FALSE | 4mm x 4mm N52 Magnet | 1 | 10.9 | https://www.patelmagnets.com/shop/4-x-4mm-neodymium-magnet/?gad_source=1
 |  | Total Price | Rs. | 1084.91

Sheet: Toolhead
Ordered | Arrived | Item | Quantity | Price | URL/Link | Notes
FALSE | FALSE | Fasteners
FALSE | FALSE | M3 Heat Set Inserts Voron Style | 9 | 7 | https://dc3d.in/shop/hardwares/m3-heat-set-insert/
FALSE | FALSE | M3 Hex Nut | 3 | 0.59 | https://omrook.com/fasteners/nut/hex-nut/m3-3mm-hex-nut-white/
FALSE | FALSE | M3 Square Nut - thin | 2 | 0.83 | https://omrook.com/fasteners/nut/square-nut/m3-square-nut-100-pcs/
FALSE | FALSE | M3 x 12mm SHCS | 3 | 1.65 | https://omrook.com/fasteners/allen-bolts/shcs-allen/ss-allen-bolt-m3-x-12mm-dia.-3mm-length-12mm-stainless-steel-ss202-socket-head-cap-screws/
FALSE | FALSE | M3 x 40mm SHCS | 1 | 5.9 | https://omrook.com/fasteners/allen-bolts/shcs-allen/ss-allen-bolt-m3-x-40mm-dia.-3mm-length-40mm-stainless-steel-ss202-socket-head-cap-screws/
FALSE | FALSE | M3 x 8mm SHCS | 1 | 1.65 | https://omrook.com/fasteners/allen-bolts/shcs-allen/ss-allen-bolt-m3-x-8mm-dia.-3mm-length-8mm-stainless-steel-ss202-socket-head-cap-screws/
FALSE | FALSE | M3 x 16mm SHCS | 3 | 1.42 | https://omrook.com/fasteners/allen-bolts/shcs-allen/ss-allen-bolt-m3-x-16mm-dia.-3mm-length-16mm-stainless-steel-ss202-socket-head-cap-screws/
FALSE | FALSE | M3 x 25mm SHCS | 3 | 2.95 | https://omrook.com/fasteners/allen-bolts/shcs-allen/ss-allen-bolt-m3-x-25mm-dia.-3mm-length-25mm-stainless-steel-ss202-socket-head-cap-screws/
FALSE | FALSE | M3 x 30mm SHCS | 1 | 3.3 | https://omrook.com/fasteners/allen-bolts/shcs-allen/ss-allen-bolt-m3-x-30mm-dia.-3mm-length-30mm-stainless-steel-ss202-socket-head-cap-screws/
FALSE | FALSE | M3 x 12 Flat Headed | 2 | 70 | https://robu.in/product/easymech-ss-304-csk-countersunk-philips-head-m3-x-12-mm-bolt-25-pcs/?gad_source=1 | Set of 25
FALSE | FALSE | M3 x 8 BHCS | 3 | 0.83 | https://omrook.com/fasteners/allen-bolts/button-allen/ss-button-allen-m3-x-8mm-dia.-3mm-length-8mm-stainless-steel-ss202-allen-socket-button-screws/
FALSE | FALSE | M3 x 6mm SHCS | 2 | 0.71 | https://omrook.com/fasteners/allen-bolts/button-allen/ss-button-allen-m3-x-6mm-dia.-3mm-length-6mm-stainless-steel-ss202-allen-socket-button-screws/
FALSE | FALSE
FALSE | FALSE | Extruder & Electronics
FALSE | FALSE | Nema 14 LDO Round Motor 10 teeth | 1 | 799 | https://novo3d.in/nema14-stepper-motor/ (https://www.bondtech.se/product/nema14-round-20mm-pancake-motor/)
FALSE | FALSE | Triangle Lab TD6S Hotend 24V | 1 | 2299 | https://novo3d.in/bambu-lab/?swcfpc=1 | (Just a place holder, look at international for proper part)Any hotend with Dragon style top mounting holes will work with mods to the parts cooling fan for nozzle alignment
FALSE | FALSE | 3010 Axial Fan 24V | 1 | 75 | https://robu.in/product/dc-24v-3010-hydraulic-cooling-fan-with-xh2-54-2p-30cm-cable-size303010mm/?gad_source=1
FALSE | FALSE | 4020 Blower Fan 24V | 1 | 208 | https://robu.in/product/dc-24v-4020-hydraulic-centrifugal-fan-with-xh2-54-2p-30cm-cable-size404020mm/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
FALSE | FALSE | BMG Dual Extruder Gear set | 1 | 399 | https://novo3d.in/bmg-gear/?swcfpc=1
FALSE | FALSE | EBB 36 Toolhead Board | 1 | 1779 | https://novo3d.in/bigtreetech-ebb36-canbus/?swcfpc=1
FALSE | FALSE | Optical Endstop Switch | 1 | 54 | https://robu.in/product/optical-endstop-light-control-limit-optical-switch/
FALSE | FALSE | Neopixel LED | 1 | 212 | https://robu.in/product/ws2812b-rgb-addressable-led-module/?gad_source=1
FALSE | FALSE |  | 1
FALSE | FALSE | Hardware
FALSE | FALSE | MGN12 Rails 35mm - Cut as per provided guide | 2 | 2699 | https://novo3d.in/mgn12h-linear-rail/ can find used rails for a lot cheaper | 100mm Rail per tool is required to obtain 2x35mm cuts
FALSE | FALSE | LM5UU Bearing | 1 | 89 | https://www.flyrobo.in/lm5uu-5mm-linear-motion-bearing-for-3d-printer
FALSE | FALSE | PC4-01 Pneumatic connector | 1 | 27 | https://robu.in/product/pc4-01-pneumatic-push-for-v6-bowden-extruders-4mm-tube-j-head-fitting
FALSE | FALSE | M3 x10mm Spacers | 3 | 100 | https://thinkrobotics.com/products/aluminium-spacers-pack-of-10?variant=39715551314006
FALSE | FALSE | 6mm x 3mm N52 Magnets | 3 | 20 | https://www.patelmagnets.com/shop/6-x-3mm-neodymium-magnets
FALSE | FALSE | M5x24mm Dowel Pin / M5x25mm Dowel Pin | 1 | 85 | https://www.3dprintronics.com/products/M5-Dowel-Pin-Straight-Type-MISUMI-p545184955
FALSE | FALSE | M3x20 Dowel Pin | 2 | 85 | https://www.3dprintronics.com/products/M3-Dowel-Pin-Straight-Type-MISUMI-p551575791
FALSE | FALSE | MR63ZZ Bearing | 2 | 870 | https://amzn.in/d/e7LxKSf Price is For moq Actuall price for qty is only Rs.174 (https://www.3dprintronics.com/products/M3-Dowel-Pin-Straight-Type-MISUMI-p551575791) | (Place Holder)
FALSE | FALSE | M3x16 Dowel Pin | 2 | 75 | https://robocraze.com/products/16mm-alloy-steel-dowel-pins-pack-of-10
FALSE | FALSE | 6mm x 6mm N52 magnet | 1 | 28 | https://www.patelmagnets.com/shop/6-x-6mm-neodymium-magnets/?attribute_pa_grade=n52
FALSE | FALSE | Hall Effect Sensor - AH3364Q | 2
FALSE | FALSE | M4 x16mm Dowel Pin | 2 | 200 | https://thinkrobotics.com/products/stainless-steel-dowel-pins-assembly-pins-pack-of-10?variant=39636812496982
FALSE | FALSE | M2.5 x 12 Socket Heads (For hotend mounting) | 4 | 20 | https://www.fastdep.in/product/pan-head-screw-m2-5x12mm/ | place holder)
FALSE | FALSE | PTFE Tube | 1 |  |  | Cut to length based on hotend - decrease measured length by 3mm to allow for z probe movement
FALSE | FALSE | 5mm - 6mm OD Spring - 4mm length - 0.5mm wire | 1 | 90.86 | Heat Bed Spacer Spring for 3D Printer UM2 Ultimaker2 (4Pcs) – RoboticsDNA (https://roboticsdna.in/product/heat-bed-spacer-spring-for-3d-printer-um2-ultimaker2-4pcs/) | Cut from larger spring - 4 loops
FALSE | FALSE
FALSE | FALSE
FALSE | FALSE | KInematic Coupling
FALSE | FALSE | M5 Acorn Nut | 3 | 30 | https://robu.in/product/easymech-m5-ms-dome-nut-acorn-nut-25-pcs/?
FALSE | FALSE | M5 x 6mm Heatset Inserts (Voron Knurled Type) | 3 |  | https://www.partsbuilt.com/m5-heat-set-thread-insert-6mm-long-4-pack/
FALSE | FALSE | M5x12mm Set Screws | 3 | 10 | https://robu.in/product/easymech-m5-x-12mm-socket-set-screws-allen-grub-10pcs/
FALSE | FALSE
FALSE | FALSE | Superglue
FALSE | FALSE | Loctite Thread Locker
FALSE | FALSE | Glue Gun (for umbilical positioning)
 |  | Total Price | Rs. | 14802.11

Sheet: All Parts
Ordered | Arrived | Item | Quantity | Price | URL/Link
FALSE | FALSE | M4 x 30 SHCS | 2 | 3.07 | https://omrook.com/fasteners/allen-bolts/shcs-allen/ss-allen-bolt-m4-x-30mm-dia.-4mm-length-30mm-stainless-steel-ss202-socket-head-cap-screws/
FALSE | FALSE | 6mmx3mm N52 magnets | 2 | 20 | https://www.patelmagnets.com/shop/6-x-3mm-neodymium-magnets/
FALSE | FALSE | 4mm x 4mm N52 magnets | 1 | 10.9 | https://www.patelmagnets.com/shop/4-x-4mm-neodymium-magnet/
FALSE | FALSE | 8mm x 5mm N52 magnets | 2 | 33 | https://www.patelmagnets.com/shop/8-x-5mm-neodymium-magnet/
FALSE | FALSE | M4 x 8mm Heatset Inserts | 2 | 50 | https://robu.in/product/m4-x-8-mm-brass-heat-set-threaded-round-insert-nut-25-pcs/ | Not ideal inserts. Try to use knurled like this: https://amzn.in/d/4WZXAzH
FALSE | FALSE | M4 Washer | 2 | 0.59 | https://omrook.com/fasteners/washer/flate-washer/m4-washer-dia-4mm-100-pcs/
FALSE | FALSE | M3 x 75mm Steel Rod | 2 | 100 | https://robocraze.com/products/300mm-stainless-steel-rod?variant=40193979154585&currency=INR | One Rod is 300mm, you will need to cut it to size
FALSE | FALSE | M4 x 95mm Steel Rod | 2 | 124 | https://roboticsdna.in/product/4mm-dia-115mm-long-chrome-plated-smooth-rod | One Rod is 115mm, you will need to cut it to size
FALSE | FALSE | 0.3mm -0.45mm Feeler Gauge Strip | 1 | 369 | https://amzn.in/d/dUbM6hw It is a whole set of feeler guages, you can find cheaper individual one locally | Full set of feeler gauges
FALSE | FALSE | M3 x 25mm SHCS | 1 | 2.83 | https://omrook.com/fasteners/allen-bolts/shcs-allen/ss-allen-bolt-m4-x-25mm-dia.-4mm-length-25mm-stainless-steel-ss202-socket-head-cap-screws/
FALSE | FALSE | M3 Washer | 1 | 0.59 | https://omrook.com/fasteners/washer/flate-washer/m3-washer-zink-white-dia-3mm-100-pcs/
FALSE | FALSE | M3 T Nut Hammer Head Drop in | 1 | 6.9 | https://novo3d.in/hammernut/
FALSE | FALSE | M5 x10 BHCS | 2 | 2.36 | https://omrook.com/fasteners/allen-bolts/shcs-allen/ss-allen-bolt-m5-x-10mm-dia.-5mm-length-10mm-stainless-steel-ss202-socket-head-cap-screws/
FALSE | FALSE | M5 T Nut Hammer Head Drop in | 2 | 6.9 | https://novo3d.in/hammernut/
FALSE | FALSE | Silicone Nozzle Cleaner | 1 | 53 | https://amzn.in/d/6Rx3F1c
FALSE | FALSE | UM Bed Spring 6MM OD / 5MM ID | 8 | 90.86 | Heat Bed Spacer Spring for 3D Printer UM2 Ultimaker2 (4Pcs) – RoboticsDNA (https://roboticsdna.in/product/heat-bed-spacer-spring-for-3d-printer-um2-ultimaker2-4pcs/)
FALSE | FALSE | M3 x 16 Dowel Pins | 6 | 19 | https://thinkrobotics.com/products/stainless-steel-dowel-pins-assembly-pins-pack-of-10?variant=39636812300374
FALSE | FALSE | M3 X 20 Dowel Pins | 6 | 19 | https://thinkrobotics.com/products/stainless-steel-dowel-pins-assembly-pins-pack-of-10?variant=39636812333142
FALSE | FALSE | M3 x 30 Dowel Pins | 4 | 22.9 | https://thinkrobotics.com/products/stainless-steel-dowel-pins-assembly-pins-pack-of-10?variant=39636812398678
FALSE | FALSE | M3 x16 Socket Head bolt | 2 | 1.42 | SS Allen Bolt M3 x 16mm, Dia. 3mm, Length 16mm, Stainless Steel (SS202) Socket Head Cap Screws from India Local Shop and Omrook (https://omrook.com/fasteners/allen-bolts/shcs-allen/ss-allen-bolt-m3-x-16mm-dia.-3mm-length-16mm-stainless-steel-ss202-socket-head-cap-screws/)
FALSE | FALSE | M3 x 20 Socket Head Bolt | 5 | 2.6 | SS Allen Bolt M3 x 20mm, Dia. 3mm, Length 20mm, Stainless Steel (SS202) Socket Head Cap Screws (https://omrook.com/fasteners/allen-bolts/shcs-allen/ss-allen-bolt-m3-x-20mm-dia.-3mm-length-20mm-stainless-steel-ss202-socket-head-cap-screws/)
FALSE | FALSE | M3 Hex Nut | 3 | 0.59 | M3 (3mm) Hex Nut White from India Local Shop and Omrook (https://omrook.com/fasteners/nut/hex-nut/m3-3mm-hex-nut-white/)
FALSE | FALSE | M3 Square Nut - 2mm thick | 4 | 0.83 | M3 Square Nut from India Local Shop and Omrook (https://omrook.com/fasteners/nut/square-nut/m3-square-nut-100-pcs/)
FALSE | FALSE | M3 x 8 Socket head Bolt | 4 | 1.65 | SS Allen Bolt M3 x 8mm, Dia. 3mm, Length 8mm, Stainless Steel (SS202) Socket Head Cap Screws (https://omrook.com/fasteners/allen-bolts/shcs-allen/ss-allen-bolt-m3-x-8mm-dia.-3mm-length-8mm-stainless-steel-ss202-socket-head-cap-screws/)
FALSE | FALSE | 4mm x 4mm N52 Magnet | 1 | 10.9 | https://www.patelmagnets.com/shop/4-x-4mm-neodymium-magnet/?gad_source=1
FALSE | FALSE | Fasteners
FALSE | FALSE | M3 Heat Set Inserts Voron Style | 9 | 7 | https://dc3d.in/shop/hardwares/m3-heat-set-insert/
FALSE | FALSE | M3 Hex Nut | 3 | 0.59 | https://omrook.com/fasteners/nut/hex-nut/m3-3mm-hex-nut-white/
FALSE | FALSE | M3 Square Nut - thin | 2 | 0.83 | https://omrook.com/fasteners/nut/square-nut/m3-square-nut-100-pcs/
FALSE | FALSE | M3 x 12mm SHCS | 3 | 1.65 | https://omrook.com/fasteners/allen-bolts/shcs-allen/ss-allen-bolt-m3-x-12mm-dia.-3mm-length-12mm-stainless-steel-ss202-socket-head-cap-screws/
FALSE | FALSE | M3 x 40mm SHCS | 1 | 5.9 | https://omrook.com/fasteners/allen-bolts/shcs-allen/ss-allen-bolt-m3-x-40mm-dia.-3mm-length-40mm-stainless-steel-ss202-socket-head-cap-screws/
FALSE | FALSE | M3 x 8mm SHCS | 1 | 1.65 | https://omrook.com/fasteners/allen-bolts/shcs-allen/ss-allen-bolt-m3-x-8mm-dia.-3mm-length-8mm-stainless-steel-ss202-socket-head-cap-screws/
FALSE | FALSE | M3 x 16mm SHCS | 3 | 1.42 | https://omrook.com/fasteners/allen-bolts/shcs-allen/ss-allen-bolt-m3-x-16mm-dia.-3mm-length-16mm-stainless-steel-ss202-socket-head-cap-screws/
FALSE | FALSE | M3 x 25mm SHCS | 3 | 2.95 | https://omrook.com/fasteners/allen-bolts/shcs-allen/ss-allen-bolt-m3-x-25mm-dia.-3mm-length-25mm-stainless-steel-ss202-socket-head-cap-screws/
FALSE | FALSE | M3 x 30mm SHCS | 1 | 3.3 | https://omrook.com/fasteners/allen-bolts/shcs-allen/ss-allen-bolt-m3-x-30mm-dia.-3mm-length-30mm-stainless-steel-ss202-socket-head-cap-screws/
FALSE | FALSE | M3 x 12 Flat Headed | 2 | 70 | https://robu.in/product/easymech-ss-304-csk-countersunk-philips-head-m3-x-12-mm-bolt-25-pcs/?gad_source=1 | Set of 25
FALSE | FALSE | M3 x 8 BHCS | 3 | 0.83 | https://omrook.com/fasteners/allen-bolts/button-allen/ss-button-allen-m3-x-8mm-dia.-3mm-length-8mm-stainless-steel-ss202-allen-socket-button-screws/
FALSE | FALSE | M3 x 6mm SHCS | 2 | 0.71 | https://omrook.com/fasteners/allen-bolts/button-allen/ss-button-allen-m3-x-6mm-dia.-3mm-length-6mm-stainless-steel-ss202-allen-socket-button-screws/
FALSE | FALSE
FALSE | FALSE | Extruder & Electronics
FALSE | FALSE | Nema 14 LDO Round Motor 10 teeth | 1 | 799 | https://novo3d.in/nema14-stepper-motor/ (https://www.bondtech.se/product/nema14-round-20mm-pancake-motor/)
FALSE | FALSE | Triangle Lab TD6S Hotend 24V | 1 | 2299 | https://novo3d.in/bambu-lab/?swcfpc=1 | (Just a place holder, look at international for proper part)Any hotend with Dragon style top mounting holes will work with mods to the parts cooling fan for nozzle alignment
FALSE | FALSE | 3010 Axial Fan 24V | 1 | 75 | https://robu.in/product/dc-24v-3010-hydraulic-cooling-fan-with-xh2-54-2p-30cm-cable-size303010mm/?gad_source=1
FALSE | FALSE | 4020 Blower Fan 24V | 1 | 208 | https://robu.in/product/dc-24v-4020-hydraulic-centrifugal-fan-with-xh2-54-2p-30cm-cable-size404020mm/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
FALSE | FALSE | BMG Dual Extruder Gear set | 1 | 399 | https://novo3d.in/bmg-gear/?swcfpc=1
FALSE | FALSE | EBB 36 Toolhead Board | 1 | 1779 | https://novo3d.in/bigtreetech-ebb36-canbus/?swcfpc=1
FALSE | FALSE | Optical Endstop Switch | 1 | 54 | https://robu.in/product/optical-endstop-light-control-limit-optical-switch/
FALSE | FALSE | Neopixel LED | 1 | 212 | https://robu.in/product/ws2812b-rgb-addressable-led-module/?gad_source=1
FALSE | FALSE |  | 1
FALSE | FALSE | Hardware
FALSE | FALSE | MGN12 Rails 35mm - Cut as per provided guide | 2 | 2699 | https://novo3d.in/mgn12h-linear-rail/ can find used rails for a lot cheaper | 100mm Rail per tool is required to obtain 2x35mm cuts
FALSE | FALSE | LM5UU Bearing | 1 | 89 | https://www.flyrobo.in/lm5uu-5mm-linear-motion-bearing-for-3d-printer
FALSE | FALSE | PC4-01 Pneumatic connector | 1 | 27 | https://robu.in/product/pc4-01-pneumatic-push-for-v6-bowden-extruders-4mm-tube-j-head-fitting
FALSE | FALSE | M3 x10mm Spacers | 3 | 100 | https://thinkrobotics.com/products/aluminium-spacers-pack-of-10?variant=39715551314006
FALSE | FALSE | 6mm x 3mm N52 Magnets | 3 | 20 | https://www.patelmagnets.com/shop/6-x-3mm-neodymium-magnets
FALSE | FALSE | M5x24mm Dowel Pin / M5x25mm Dowel Pin | 1 | 85 | https://www.3dprintronics.com/products/M5-Dowel-Pin-Straight-Type-MISUMI-p545184955
FALSE | FALSE | M3x20 Dowel Pin | 2 | 85 | https://www.3dprintronics.com/products/M3-Dowel-Pin-Straight-Type-MISUMI-p551575791
FALSE | FALSE | MR63ZZ Bearing | 2 | 870 | https://amzn.in/d/e7LxKSf Price is For moq Actuall price for qty is only Rs.174 (https://www.3dprintronics.com/products/M3-Dowel-Pin-Straight-Type-MISUMI-p551575791) | (Place Holder)
FALSE | FALSE | M3x16 Dowel Pin | 2 | 75 | https://robocraze.com/products/16mm-alloy-steel-dowel-pins-pack-of-10
FALSE | FALSE | 6mm x 6mm N52 magnet | 1 | 28 | https://www.patelmagnets.com/shop/6-x-6mm-neodymium-magnets/?attribute_pa_grade=n52
FALSE | FALSE | Hall Effect Sensor - AH3364Q | 2
FALSE | FALSE | M4 x16mm Dowel Pin | 2 | 200 | https://thinkrobotics.com/products/stainless-steel-dowel-pins-assembly-pins-pack-of-10?variant=39636812496982
FALSE | FALSE | M2.5 x 12 Socket Heads (For hotend mounting) | 4 | 20 | https://www.fastdep.in/product/pan-head-screw-m2-5x12mm/ | place holder)
FALSE | FALSE | PTFE Tube | 1 |  |  | Cut to length based on hotend - decrease measured length by 3mm to allow for z probe movement
FALSE | FALSE | 5mm - 6mm OD Spring - 4mm length - 0.5mm wire | 1 | 90.86 | Heat Bed Spacer Spring for 3D Printer UM2 Ultimaker2 (4Pcs) – RoboticsDNA (https://roboticsdna.in/product/heat-bed-spacer-spring-for-3d-printer-um2-ultimaker2-4pcs/) | Cut from larger spring - 4 loops
FALSE | FALSE
FALSE | FALSE
FALSE | FALSE | KInematic Coupling
FALSE | FALSE | M5 Acorn Nut | 3 | 30 | https://robu.in/product/easymech-m5-ms-dome-nut-acorn-nut-25-pcs/?
FALSE | FALSE | M5 x 6mm Heatset Inserts (Voron Knurled Type) | 3 |  | https://www.partsbuilt.com/m5-heat-set-thread-insert-6mm-long-4-pack/
FALSE | FALSE | M5x12mm Set Screws | 3 | 10 | https://robu.in/product/easymech-m5-x-12mm-socket-set-screws-allen-grub-10pcs/
FALSE | FALSE
FALSE | FALSE | Superglue
FALSE | FALSE | Loctite Thread Locker
FALSE | FALSE | Glue Gun (for umbilical positioning)
 |  | Total Price | Rs. | 17010.08

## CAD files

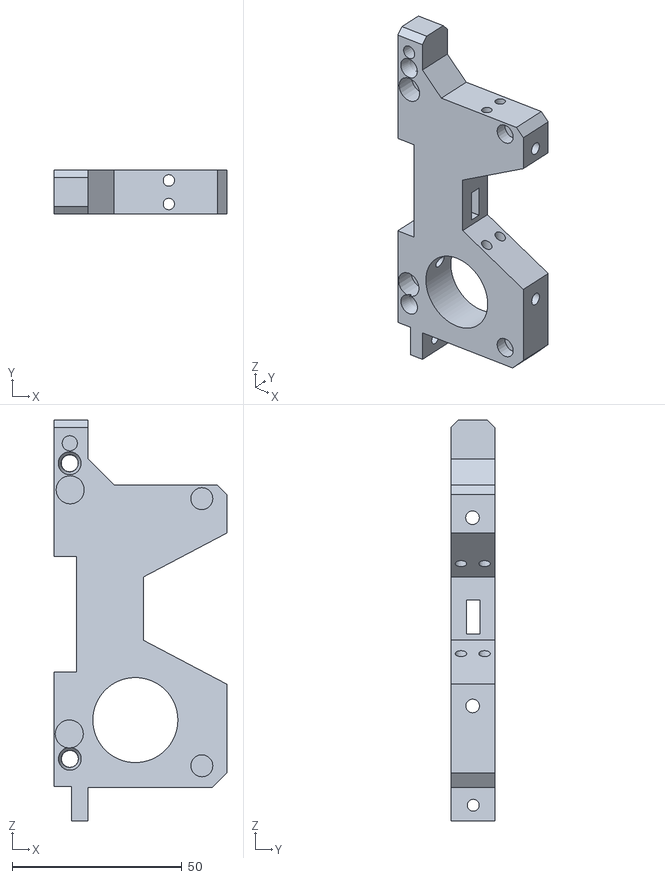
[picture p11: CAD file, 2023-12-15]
STL/Dock/dock-main.stl
50.8 x 12.9 x 118.0

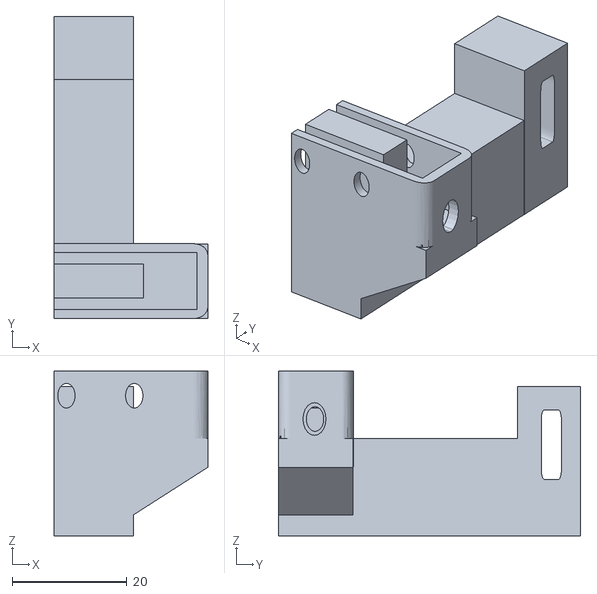
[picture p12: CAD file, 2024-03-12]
STL/Dock/nozzle-scrubber.stl
26.7 x 52.5 x 28.7

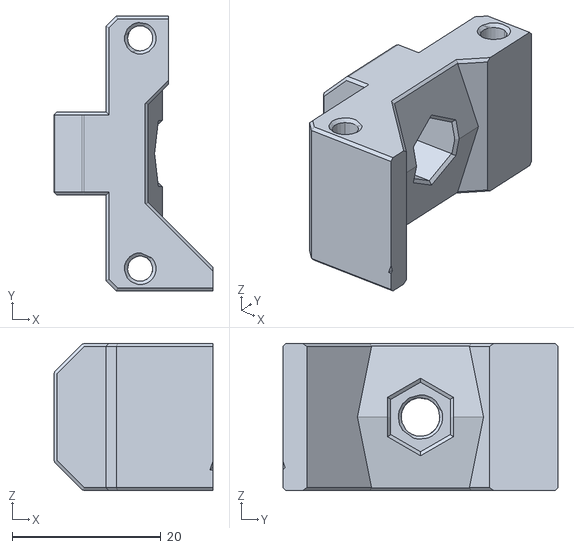
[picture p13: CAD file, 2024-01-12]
STL/Gantry/ab-motor-mount-tensioner-right.stl
21.4 x 37.0 x 19.8

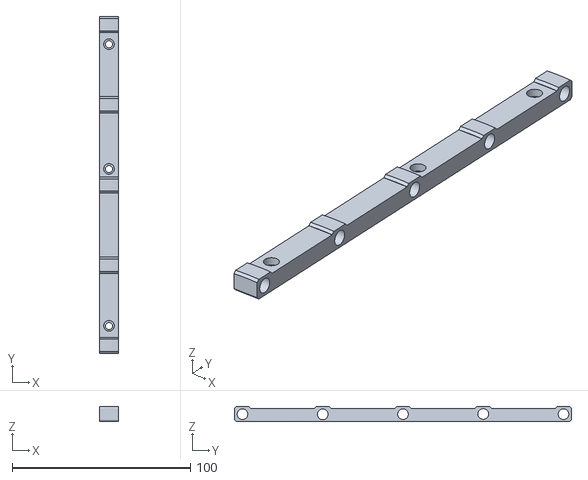
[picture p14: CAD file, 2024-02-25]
STL/Misc/ptfe-route-holder-p2.stl
10.9 x 188.9 x 8.55

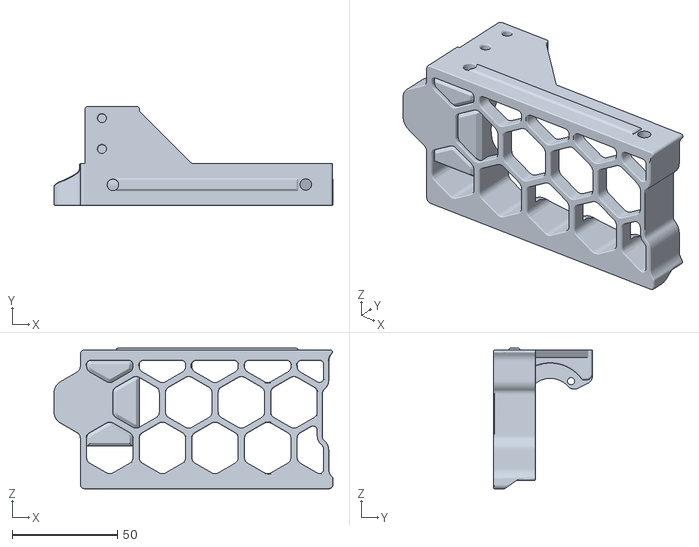
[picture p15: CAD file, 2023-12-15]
STL/Quad Z/geared-servo-mount-a x 2.stl
132.5 x 47.1 x 66.8

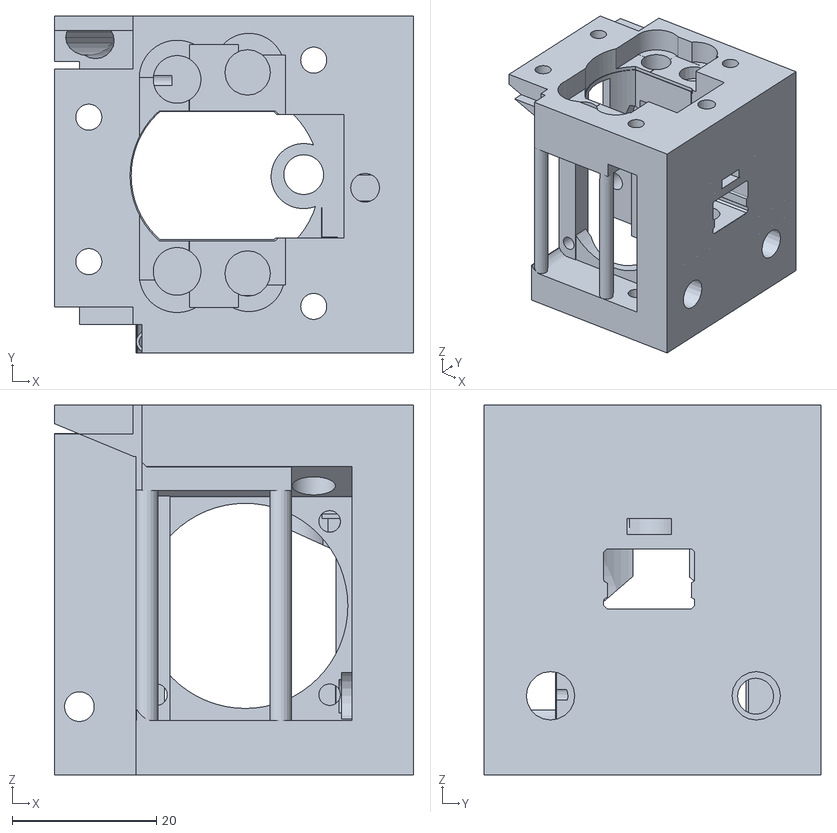
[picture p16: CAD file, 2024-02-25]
STL/Toolhead/toolhead-bottom.stl
49.7 x 46.7 x 51.2

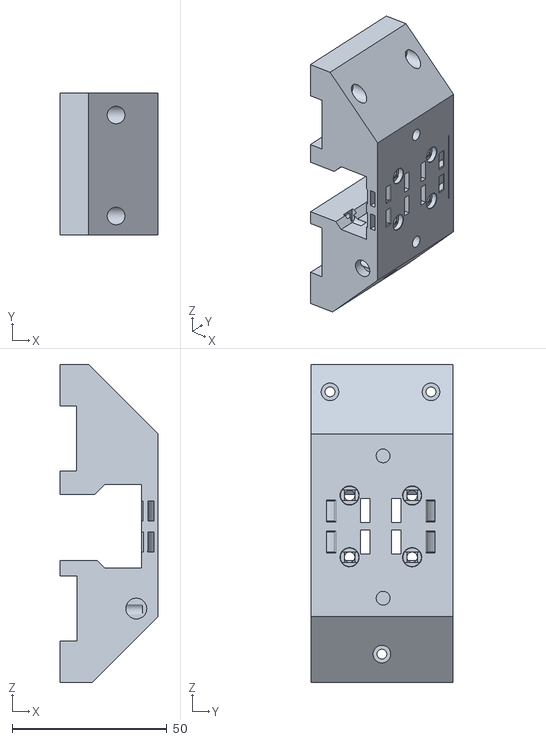
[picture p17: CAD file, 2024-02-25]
STL/ToolLock/carriage-mgn12-integrated--belt-groove.stl
31.8 x 46.0 x 102.8

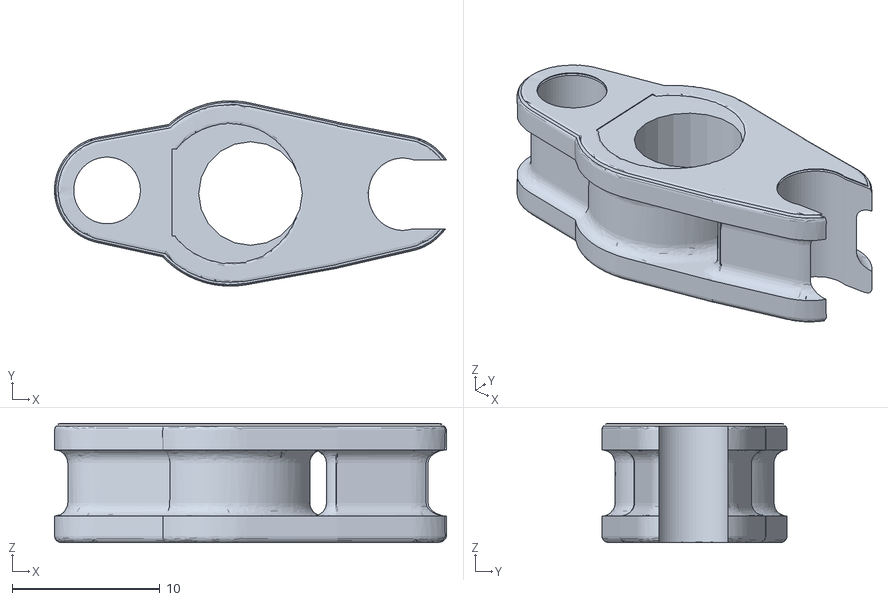
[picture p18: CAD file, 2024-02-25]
STL/Dock/wire-loom-clip x 5.stl
26.5 x 12.5 x 8.06

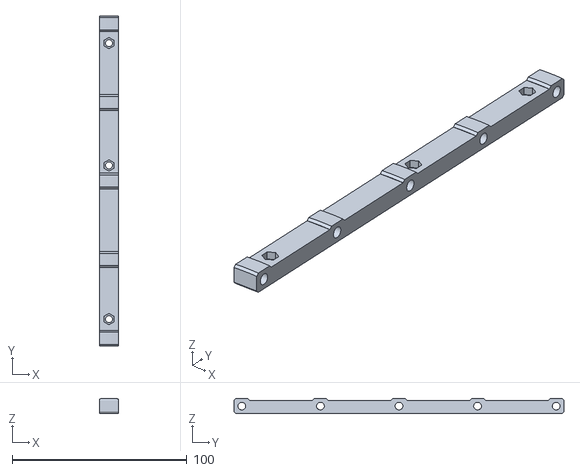
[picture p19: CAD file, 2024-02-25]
STL/Misc/ptfe-route-holder-p1.stl
10.9 x 188.9 x 8.55

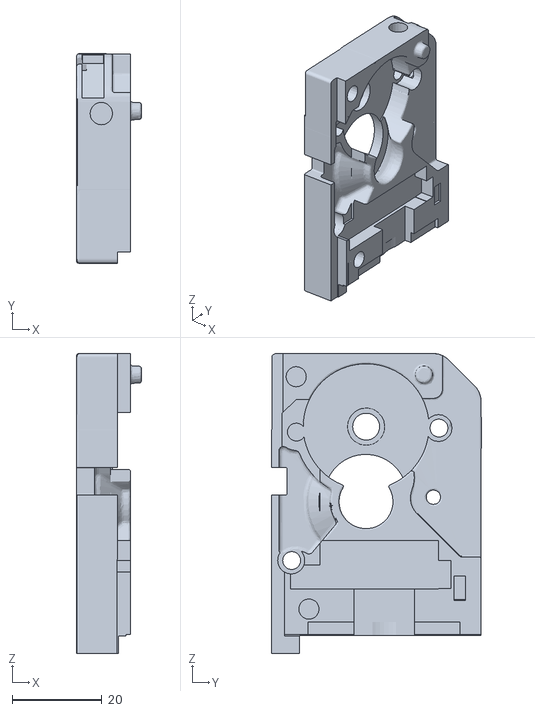
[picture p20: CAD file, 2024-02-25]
STL/Toolhead/toolhead-top-2.stl
14.5 x 46.7 x 66.8

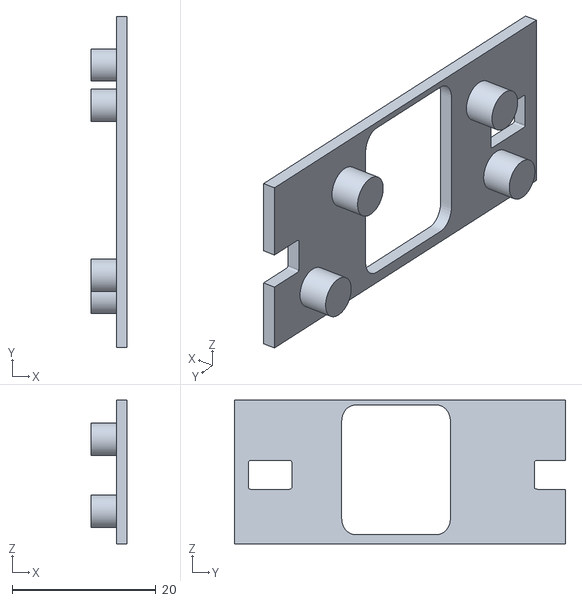
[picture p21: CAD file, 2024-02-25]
STL/ToolLock/spring-spacer-bottom.stl
5.00 x 46.0 x 20.0

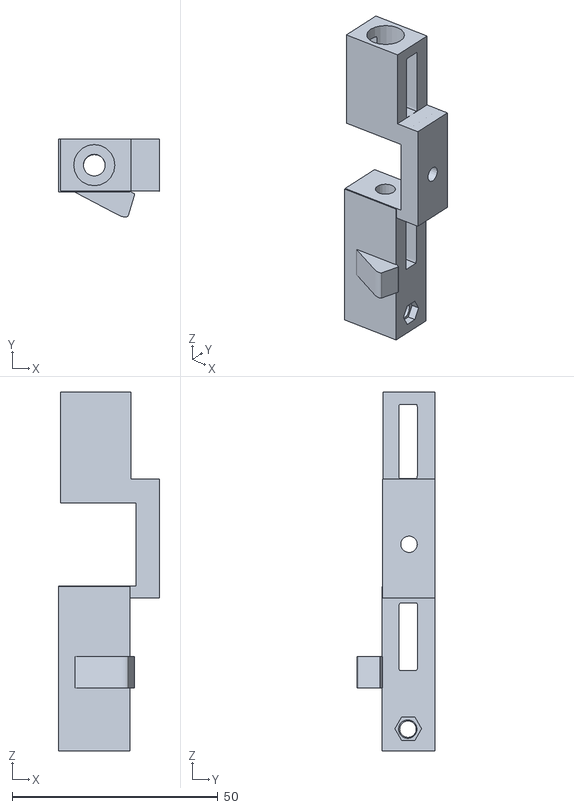
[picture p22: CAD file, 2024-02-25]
STL/Dock/dock-2020-mount.stl
24.4 x 19.0 x 87.2

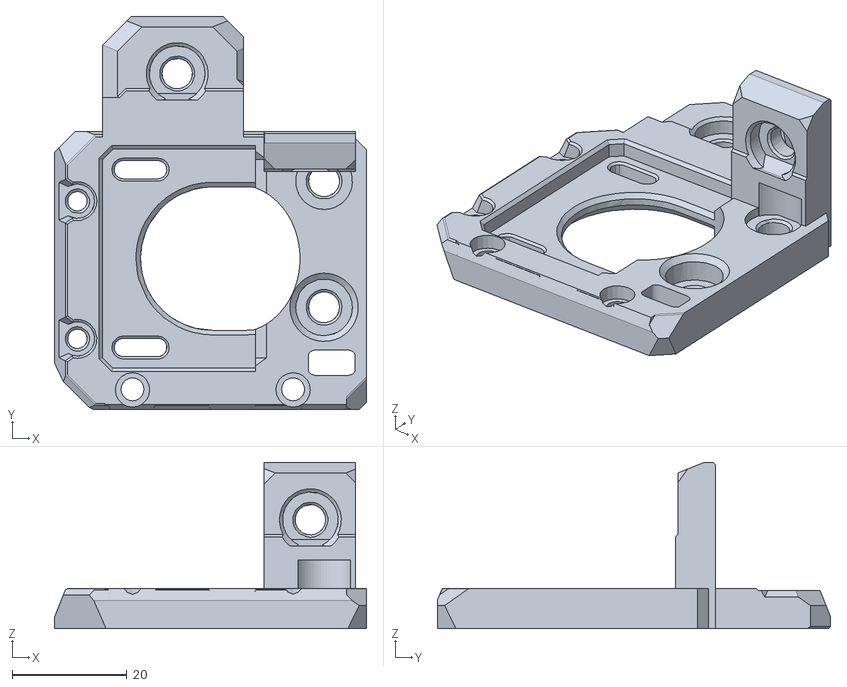
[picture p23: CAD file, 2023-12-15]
STL/Gantry/ab-motor-mount-left-1.stl
54.4 x 68.6 x 29.0

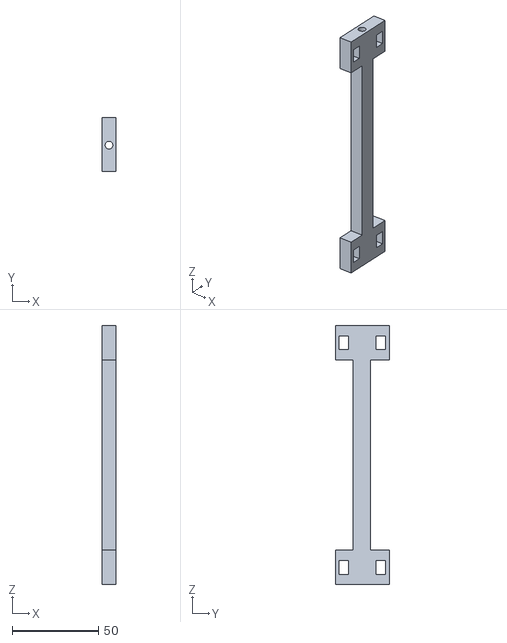
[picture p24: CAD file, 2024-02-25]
STL/Misc/ab-motor-extrusion-spacer-jig.stl
8.00 x 31.0 x 150.0

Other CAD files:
STL/Gantry/ab-motor-mount-tensioner-left.stl
STL/Quad Z/geared-servo-mount-b x 2.stl
STL/Quad Z/z-lder-front-left.stl
STL/Toolhead/ebb36-mount.stl
STL/Dock/dock-oozeshield-mount.stl
STL/Dock/dock-oozeshield-slider.stl
STL/Dock/dock-oozeshield-strip-holder.stl
STL/Dock/dock-wireloom-extrusion-holder.stl
STL/Gantry/ab-motor-mount-left-2.stl
STL/Gantry/ab-motor-mount-left-3.stl
STL/Gantry/ab-motor-mount-right-1.stl
STL/Gantry/ab-motor-mount-right-2stl.stl
STL/Gantry/ab-motor-mount-right-3.stl
STL/Gantry/ab-motor-mount-spacer x 2.stl
STL/Gantry/front-idler-left-1.stl
STL/Gantry/front-idler-left-2stl.stl
STL/Gantry/front-idler-right-1.stl
STL/Gantry/front-idler-right-2.stl
STL/Gantry/xy-joint-left-1.stl
STL/Gantry/xy-joint-left-2.stl
STL/Gantry/xy-joint-right-1.stl
STL/Gantry/xy-joint-right-2.stl
STL/Misc/mgn12-cut-guide.stl
STL/Misc/tool-dock-spacer.stl
STL/Quad Z/bed-mount-a x2.stl
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

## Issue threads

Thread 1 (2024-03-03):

Any idea how it could work with a voron v2.4?

d0m1n1qu3, 2024-03-03:
Do you have any idea how it could work with a voron v2.4?
Because it has a flying gantry and a z cablechain .. so i dont know how to mount the mounts

may be you have an idea and some kind of picture to show how :-)

thanks and greetings

ankurv2k6, 2024-03-05:
I am working on a port to 2.4 - will share soon once ready.

Ericdmch, 2024-12-20:
Where would I mount the docks for a voron 2.4? Do I need an extra horizontal beam across the front? Thanks

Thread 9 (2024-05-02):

How to cut 35mm mgn12 ?

jiratto, 2024-05-02:
How about distance from edge to holes?

Thank you

AkeemA, 2024-05-02:
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

AkeemA, 2024-05-02:
The drawing is taken from the CAD, there's also a cutting jig in the Misc folder to make things easier

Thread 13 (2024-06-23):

BOM needs minor update (8 m3x30mm dowl pens not 4)

jhandel, 2024-06-23:
While building a tool holder I noticed that it looked like we need 4 30mm m3 dowls for the axis connector and then 2 for each of the sliders (total 8).  The BOM shows only needing 4.. I double checked your construction video and it also shows needing a total of 8.

Not a big deal but figured it was worth sharing.

Thanks

3dfiyMyLife, 2024-06-25:
Yup, just checked and you are right. Thank you for the discovery. Will try having them updated. There's a few changes as well to the toolheads as we're more towards the new V2ool toolheads now

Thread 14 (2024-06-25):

How to calibrate all nozzles z,x,y offset?

jiratto, 2024-06-25:
How to calibrate all nozzles z,x,y offset?

In case of prusa XL, It has probe.
https://youtube.com/shorts/5ZyMBhFUcWE?si=2teC6oXOfSA0gv8v

3dfiyMyLife, 2024-06-25:
Nozzles calibration is done using Nudge. Its in the github
https://github.com/zruncho3d/nudge

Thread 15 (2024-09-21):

Cant open STEP file from Daksh2.4 V2 Carriage v28.rar

Railnolds, 2024-09-21:
Hi. I can't open the STEP file from the Daksh2.4 V2 Carriage v28.rar archive in SolidWorks. Could you please check if everything is OK with this file? Other files open fine.
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

Hoda5, 2025-05-09:
Hi!! Try to use 7zip. When you open the .rar file in 7zip select the .step you need and SHIFT+ENTER. It will open the open with list, I use Fusion360 and it works. I can see you are using solidworks, so I hope it works for you too!!

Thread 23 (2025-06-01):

tools-calibrate not compatible with klipper after cc6736c

Dan3dp, 2025-06-01:
After updating klipper (and klipper-toolchanger) I run into a
Internal error on command:"TOOL_LOCATE_SENSOR"
when trying to run a calibration.
I was able to pinpoint the commit it stopped working (https://github.com/Klipper3d/klipper/commit/cc6736c3e35cb6f6e660d973be67ab4cef78ffb9) but it's a little beyond my current knowledge to find the actual reason.

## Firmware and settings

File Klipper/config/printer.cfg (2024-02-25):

# This file contains common pin mappings for the BigTreeTech GTR.
# To use this config, the firmware should be compiled for the
# STM32F407 with a "32KiB bootloader".

# The "make flash" command does not work on the GTR. Instead,
# after running "make", copy the generated "klipper/out/klipper.bin" file to a
# file named "firmware.bin" on an SD card and then restart the GTR
# with that SD card.

# See docs/Config_Reference.md for a description of parameters.

[include fluidd.cfg]
#[include adxl.cfg]

[skew_correction] 
[exclude_object]
[respond]
[tool_probe_endstop]
[gcode_arcs]

[force_move]
enable_force_move=1

[mcu]
serial: /dev/serial/by-id/usb-Klipper_stm32f446xx_25000B000E5053424E363620-if00

[printer]
kinematics: corexy
max_velocity: 400
max_accel: 12000
max_z_velocity: 300
max_z_accel: 400
square_corner_velocity: 5.0  

[input_shaper]

[pause_resume]

[display_status]

[exclude_object]

[virtual_sdcard]
path: /home/pi/printer_data/gcodes


[mcu rpi]
serial: /tmp/klipper_host_mcu

[stepper_x]
step_pin: PF13
dir_pin: !PF12
enable_pin: !PF14
microsteps:32
rotation_distance: 40
full_steps_per_rotation: 200
position_min: 0
position_endstop: 0
position_max: 365
homing_speed: 100
second_homing_speed: 5
homing_positive_dir: false
endstop_pin: !PG9
homing_retract_dist: 5


[stepper_y]
step_pin: PG0
dir_pin: !PG1
enable_pin: !PF15
microsteps: 32
rotation_distance: 40
full_steps_per_rotation: 200
endstop_pin: !PG6
position_endstop: 0
position_max: 375
position_min: 0
homing_speed: 100
homing_retract_dist: 5
second_homing_speed: 5
homing_positive_dir: false



[stepper_z]
step_pin: PE6
dir_pin: PA14
enable_pin: !PE0
rotation_distance: 40
gear_ratio: 57:11   
microsteps: 32
full_steps_per_rotation: 200	#200 for 1.8 degree, 400 for 0.9 degree
endstop_pin: probe:z_virtual_endstop
position_max: 300
position_min: -5
homing_speed: 30
second_homing_speed: 2


[stepper_z1]
step_pin: PF9
dir_pin: !PF10
enable_pin: !PG2
rotation_distance: 40
gear_ratio: 57:11   
microsteps: 32
full_steps_per_rotation: 200	#200 for 1.8 degree, 400 for 0.9 degree


[stepper_z2]
step_pin: PC13
dir_pin: !PF0
enable_pin: !PF1
rotation_distance: 40
gear_ratio: 57:11   
microsteps: 32
full_steps_per_rotation: 200	#200 for 1.8 degree, 400 for 0.9 degree


[stepper_z3]
step_pin: PE2
dir_pin: !PE3
enable_pin: !PD4
rotation_distance: 40
gear_ratio: 57:11   
microsteps: 32
full_steps_per_rotation: 200	#200 for 1.8 degree, 400 for 0.9 degree




########################################
# tmc2209 configuration
########################################

[tmc2209 stepper_x]
uart_pin: PC4
run_current: 1.3
interpolate: False
sense_resistor: 0.110



[tmc2209 stepper_y]
uart_pin: PD11
run_current: 1.3
interpolate: False
sense_resistor: 0.110



[tmc2209 stepper_z]
uart_pin: PD3
run_current: 1.0
interpolate: False
sense_resistor: 0.110



[tmc2209 stepper_z1]
uart_pin: PF2
run_current: 1.0
interpolate: False
sense_resistor: 0.110



[tmc2209 stepper_z2]
uart_pin: PE4
run_current: 1.0
interpolate: False
sense_resistor: 0.110


[tmc2209 stepper_z3]
uart_pin: PE1
run_current: 1.0
interpolate: False
sense_resistor: 0.110



[fan_generic RSCS]
##  RSCS Fans - In FAN1 Positon
pin: PD13
max_power: 1
shutdown_speed: 0
kick_start_time: 0.1
off_below: 0.10

[controller_fan driver_fan]
pin:PD12
max_power:0.5
shutdown_speed: 0
kick_start_time: 0.1
off_below: 0.10
stepper:stepper_x, stepper_y
#####################################################################
# 	Bed Heater
#####################################################################

[heater_bed]
##	SSR Pin - Z board, Fan Pin
heater_pin: PE5
sensor_type:Generic 3950
sensor_pin: PF3
##	Adjust Max Power so your heater doesn't warp your bed
max_power: 0.9
min_temp: 0
max_temp: 120
pwm_cycle_time: 0.02
control: pid
pid_kp: 58.437
pid_ki: 2.347
pid_kd: 363.769


[verify_heater heater_bed]
max_error: 180
check_gain_time: 180
heating_gain: 2


#####################################################################
# 	Probe
#####################################################################



[include calibrate-offsets.cfg]

#######################################
#### Enclosure Temp Sensor Section ####
#######################################

[temperature_sensor raspberry_pi]
sensor_type: temperature_host
min_temp: 10
max_temp: 100

[temperature_sensor octopus]
sensor_type: temperature_mcu
min_temp: 10
max_temp: 100

[neopixel cled]
##	To control Neopixel RGB in mini12864 display
pin: PB6
chain_count:60
initial_RED: 1
initial_GREEN: 1
initial_BLUE: 1
color_order:GRB


[idle_timeout]
timeout: 1800

[homing_override]
axes: z
set_position_z: 0
gcode:
    {% if printer["gcode_macro VARIABLES_LIST"].tc_state|int == 0 %} 
      G90
      G0 Z10 F4000
      G28 Y0 
      G28 X0
      G0 X165 Y140 F6000
      G28 Z0
      G0 Z40 F4000
    {% else %}
      M118 "Tool Changer in error state. Unable to continue."
    {% endif %}

[z_tilt]

z_positions:
	-50, -24
    -50, 340
    405,340
    405,-24
points:
       40, 5
       165, 265
       290, 5
    
    
#points:
  #  50, 50
  #  50,250
  #  250,250
  #  250,50
  # retry_tolerance: 0.2
    
speed: 300
horizontal_move_z: 10
retries: 5
retry_tolerance: 0.01250


[bed_mesh]
speed: 300
horizontal_move_z: 5
mesh_min: 30,20
mesh_max: 290,265
fade_end: 10.0
probe_count: 5,5
algorithm: bicubic
zero_reference_position:150,150
#relative_reference_index: 12

[include toolchanger.cfg]
#####################################################################
# 	Macros
#####################################################################

  
[gcode_macro G32]
gcode:
    BED_MESH_CLEAR
    G28
    Z_TILT_ADJUST
    G28
    G0 X175 Y175 Z20 F6000

# prime the nozzle 
[gcode_macro PRIME_LINE]
gcode: 
    #M117 Priming Line
    {% if "z" not in printer.toolhead.homed_axes %} ; G28 Home if needed
        G28             ; home
    {% endif %}
    SAVE_GCODE_STATE NAME=PRIME_LINE_state
    G90                                 ; absolute positioning
    G92 E0                              ; reset extruder
    G1 E10 F1000
    G1 Z5.0 F3000                       ; move Z Axis up
    G1 X10 Y50 Z0.2 F5000.0            ; move to start position
    G1 X10 Y175 Z0.2 F1000.0 E15     ; draw the first line
    G1 X10.4 Y175 Z0.2 F5000.0         ; move to side a little
    G1 X10.4 Y50 Z0.2 F1000.0 E30        ; draw the second line
    G92 E0                              ; reset Extruder
    G1 Z5.0 F3000                       ; move Z Axis up
    G1 X40 Y50 F2000.0 
    RESTORE_GCODE_STATE NAME=PRIME_LINE_state   
  
  
[gcode_macro PRINT_START]
#   Use PRINT_START for the slicer starting script - please customise for your slicer of choice
gcode:    
    {% if params.BED %}
        M140 S{params.BED}         ; set bed final temp
        M190 S{params.BED}         ; wait for bed final temp
    {% endif %}
   {% if params.EXTRUDER %}
        M104 S{params.EXTRUDER}    ; set extruder final temp
        M109 S{params.EXTRUDER}    ; wait for extruder final temp
    {% endif %}
    G32
    G90             ; absolute positioning
    M82             ; absolute extruder mode
    M107            ; turn fan off
    BEDMESHLOAD
    PRIME_LINE

[gcode_macro PRINT_END]
#   Use PRINT_END for the slicer ending script - please customise for your slicer of choice
gcode:

    ; Custom gcode to run at end of print
	M104 S0 		; turn off temperature
	G10 P0 R0 S0 A0	; Don't heat the tools yet. (Using G10 so SuperSlicer and PrusaSlicer recognizes we set a tool temperature)
	G10 P1 R0 S0 A0	; Don't heat the tools yet
	M140 S0 		; turn off bed
	G91 		; relative moves
	G0 Z20  		; move bed down another 30mm
	G90 		; absolute moves
    G92 E0                              ; reset extruder
	G0 X150 Y10 F30000	; Move toolhead out of the way
	SAVE_POSITION
	RSCS_OFF
    #AIR_FILTER_STOP
    BED_MESH_CLEAR

[gcode_macro NOZZLE_CLEAN]
gcode:
   # G0 E1 F500

        
[gcode_macro NOZZLE_CLEAN1]
gcode:
    SAVE_GCODE_STATE NAME=BEFORE_CLEAN
    G91
    G0 X10 F12000       ; move to nozzle brush
    G0 Y50 F12000       ; move to nozzle brush
    G0 X-20 F12000       ; move to nozzle brush
    G0 Y-50 F12000       ; move to nozzle brush
    G0 X20 F12000       ; move to nozzle brush
    G0 Y50 F12000       ; move to nozzle brush
    G0 X-20 F12000       ; move to nozzle brush
    G0 Y-50 F12000       ; move to nozzle brush
    G0 X20 F12000       ; move to nozzle brush
    G0 Y50 F12000       ; move to nozzle brush
    G0 X-10 F12000       ; move to nozzle brush
    G0 Y-50 F12000       ; move to nozzle brush
    G90   
    RESTORE_GCODE_STATE NAME=BEFORE_CLEAN


[gcode_macro PURGE]
gcode:
    SAVE_GCODE_STATE NAME=PURGE_state
    G91                 ; relative positioning
    {% for i in range(2) %}
        G1 E10 F500      ; extrude a little more
    {% endfor %}
    RESTORE_GCODE_STATE name=PURGE_state
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

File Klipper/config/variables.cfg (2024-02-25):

[Variables]
ktcc_dock_move_speed = 3000
ktcc_speed1 = 40000
ktcc_speed2 = 20000
ktcc_speed3 = 8000
ktcc_statistics_swaps = {'total_time_spent_mounting': 13997.4, 'total_time_spent_unmounting': 8850.5, 'total_toolunlocks': 6910, 'total_toollocks': 6883, 'total_toolmounts': 6881, 'total_toolunmounts': 6910}
ktcc_statistics_tool0 = {'toolmounts_completed': 1755, 'toolunmounts_completed': 1827, 'toolmounts_started': 1759, 'toolunmounts_started': 1827, 'time_selected': 58254.236275196075, 'time_heater_active': 94564.95263409615, 'time_heater_standby': 76619.51860189438, 'tracked_start_time_selected': 0, 'tracked_start_time_active': 0, 'tracked_start_time_standby': 0, 'total_time_spent_unmounting': 2639.824, 'total_time_spent_mounting': 2114.613, 'tracked_unmount_start_time': 0, 'tracked_mount_start_time': 0}
ktcc_statistics_tool1 = {'toolmounts_completed': 1420, 'toolunmounts_completed': 1409, 'toolmounts_started': 1422, 'toolunmounts_started': 1409, 'time_selected': 27032.367559671402, 'time_heater_active': 58061.207582235336, 'time_heater_standby': 48006.8974173069, 'tracked_start_time_selected': 0, 'tracked_start_time_active': 0, 'tracked_start_time_standby': 0, 'total_time_spent_unmounting': 1685.776, 'total_time_spent_mounting': 1609.197, 'tracked_unmount_start_time': 0, 'tracked_mount_start_time': 0}
ktcc_statistics_tool2 = {'toolmounts_completed': 1347, 'toolunmounts_completed': 1340, 'toolmounts_started': 1349, 'toolunmounts_started': 1340, 'time_selected': 24028.278047323227, 'time_heater_active': 44436.98944282532, 'time_heater_standby': 83658.95399165154, 'tracked_start_time_selected': 0, 'tracked_start_time_active': 0, 'tracked_start_time_standby': 0, 'total_time_spent_unmounting': 1630.295, 'total_time_spent_mounting': 3138.278, 'tracked_unmount_start_time': 0, 'tracked_mount_start_time': 0}
ktcc_statistics_tool3 = {'toolmounts_completed': 1147, 'toolunmounts_completed': 1144, 'toolmounts_started': 1149, 'toolunmounts_started': 1144, 'time_selected': 32691.270093679428, 'time_heater_active': 54482.766932964325, 'time_heater_standby': 93092.25932478905, 'tracked_start_time_selected': 0, 'tracked_start_time_active': 0, 'tracked_start_time_standby': 0, 'total_time_spent_unmounting': 1379.71, 'total_time_spent_mounting': 3113.414, 'tracked_unmount_start_time': 0, 'tracked_mount_start_time': 0}
ktcc_statistics_tool4 = {'toolmounts_completed': 1213, 'toolunmounts_completed': 1190, 'toolmounts_started': 1218, 'toolunmounts_started': 1190, 'time_selected': 34802.70572018623, 'time_heater_active': 58670.181111097336, 'time_heater_standby': 50879.47878623009, 'tracked_start_time_selected': 0, 'tracked_start_time_active': 0, 'tracked_start_time_standby': 0, 'total_time_spent_unmounting': 1515.499, 'total_time_spent_mounting': 4024.039, 'tracked_unmount_start_time': 0, 'tracked_mount_start_time': 0}
t0_lock_x = 23.4
t0_lock_y = 364.5
t0_unlock_x = 11
t0_unlock_y = 364
t0_x_offset = 0
t0_y_offset = 0.02
t0_z_offset = 1.35
t1_lock_x = 100.42
t1_lock_y = 364.5
t1_unlock_x = 88
t1_unlock_y = 364
t1_x_offset = 0.65
t1_y_offset = 0.28
t1_z_offset = 0.36
t2_lock_x = 177.35
t2_lock_y = 364.5
t2_unlock_x = 165.35
t2_unlock_y = 364
t2_x_offset = 0.13
t2_y_offset = 0.21
t2_z_offset = 0.2
t3_lock_x = 254.19
t3_lock_y = 364.5
t3_unlock_x = 242.19
t3_unlock_y = 364
t3_x_offset = 0.9
t3_y_offset = 0.45
t3_z_offset = 0.1
t4_lock_x = 330.89
t4_lock_y = 364.5
t4_unlock_x = 318.89
t4_unlock_y = 364
t4_x_offset = 0.73
t4_y_offset = 0.7
t4_z_offset = 0.3
tool_current = -1

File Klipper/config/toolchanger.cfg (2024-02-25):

# Config order: ToolGroups must come before tools that use them. Tool that are used as physical_parent must be configured before other virtual tools that use that as parent.


[include klipper_toolchanger/*.cfg]
[include tools/*.cfg]
[include calibrate-offsets.cfg]
[include status_led.cfg]
[include crash_detection.cfg]
[include dock_calibrate.cfg]
[include filament_sensors.cfg]
[include tool_usage.cfg]

# Enables saving of variables between powerdown of machine. Must be configured before [toollock].
[save_variables]
  filename:  ~/printer_data/config/variables.cfg

[toollock]
purge_on_toolchange = False          # Here we can disable all purging. When disabled it overrides all other purge options. Defaults to true. This can be turned off by a macro for automatic probing hot tools without probing them. For example when doing TAMV or ZTATP.
init_printer_to_last_tool = True   #Initialise as it was turned off, unlock tool if none was loaded or lock if one was loaded. Defaults to True
tool_lock_gcode:
  SAVE_GCODE_STATE NAME=tool_unlock_state                                         # Save gcode state
   G91 
   #XY_HIGH_TORQUE_START
   G1 X-14 F{printer.save_variables.variables['ktcc_dock_move_speed']|int}
   G1 X2 F{printer.save_variables.variables['ktcc_dock_move_speed']|int}
   #XY_HIGH_TORQUE_STOP
   RESTORE_GCODE_STATE NAME=tool_unlock_state MOVE=0                               # Restore gcode state
  
tool_unlock_gcode:
  SAVE_GCODE_STATE NAME=tool_lock_state                                           # Save gcode state
   G91 
   G1 X12 F{printer.save_variables.variables['ktcc_dock_move_speed']|int}
   #G1 X-1 F{printer.save_variables.variables['ktcc_dock_move_speed']|int}
  RESTORE_GCODE_STATE NAME=tool_lock_state MOVE=0                                 # Restore gcode state
  

# Used to group several tools with similar settings.
[toolgroup 0]
is_virtual: False            # If True then must have a physical_parent declared and shares extruder, hotend and fan with the physical_parent
pickup_gcode: 
  SUB_TOOL_PICKUP_START T={myself.name}
  SUB_TOOL_PICKUP_END T={myself.name}

dropoff_gcode:
  SUB_TOOL_DROPOFF_START T={myself.name}
  SUB_TOOL_DROPOFF_END T={myself.name}

##### Selectable tool. Must be configured after [toolgroup n].
[tool 0]
tool_group: 0                     # Must be used and configured before this tool
extruder: extruder
fan: partfan_t0
zone: 0,0,0
park: 0,0,0
offset:0,0,0
meltzonelength: 0 #18                 # Defaults to 0
idle_to_standby_time: 0.1          # Time in seconds from being parked to setting temperature to standby the temperature above. Use 0.1 to change imediatley to standby temperature. Defaults to 30
idle_to_powerdown_time: 1800       # Time in seconds from being parked to setting temperature to 0. Use something like 86400 to wait 24h if you want to disable. Defaults to 600
lazy_home_when_parking: 1           # (default: 0 - disabled) - When set to 1, will home unhomed XY axes if needed and will not move any axis if already homed and parked. 2 Will also home Z if not homed.
shaper_freq_y: 103
shaper_freq_x: 33
shaper_type_y: zv
shaper_type_x: mzv


[tool 1]
tool_group: 0                     # Must be used and configured before this tool
extruder: extruder1
zone: 0,0,0
park: 0,0,0
offset:0,0,0
fan: partfan_t1
meltzonelength: 0 #18                 # Defaults to 0
idle_to_standby_time: 0.1          # Time in seconds from being parked to setting temperature to standby the temperature above. Use 0.1 to change imediatley to standby temperature. Defaults to 30
idle_to_powerdown_time: 1800       # Time in seconds from being parked to setting temperature to 0. Use something like 86400 to wait 24h if you want to disable. Defaults to 600
lazy_home_when_parking: 1           # (default: 0 - disabled) - When set to 1, will home unhomed XY axes if needed and will not move any axis if already homed and parked. 2 Will also home Z if not homed.
shaper_freq_y: 103
shaper_freq_x: 33
shaper_type_y: zv
shaper_type_x: mzv


[tool 2]
tool_group: 0                     # Must be used and configured before this tool
extruder: extruder2
zone: 0,0,0
park: 0,0,0
offset:0,0,0
fan: partfan_t2
meltzonelength: 0 #18                 # Defaults to 0
idle_to_standby_time: 0.1          # Time in seconds from being parked to setting temperature to standby the temperature above. Use 0.1 to change imediatley to standby temperature. Defaults to 30
idle_to_powerdown_time: 1800       # Time in seconds from being parked to setting temperature to 0. Use something like 86400 to wait 24h if you want to disable. Defaults to 600
lazy_home_when_parking: 1           # (default: 0 - disabled) - When set to 1, will home unhomed XY axes if needed and will not move any axis if already homed and parked. 2 Will also home Z if not homed.
shaper_freq_y: 103
shaper_freq_x: 33
shaper_type_y: zv
shaper_type_x: mzv



[tool 3]
tool_group: 0                     # Must be used and configured before this tool
extruder: extruder3
zone: 0,0,0
park: 0,0,0
offset:0,0,0
fan: partfan_t3
meltzonelength: 0 #18                 # Defaults to 0
idle_to_standby_time: 0.1          # Time in seconds from being parked to setting temperature to standby the temperature above. Use 0.1 to change imediatley to standby temperature. Defaults to 30
idle_to_powerdown_time: 1800       # Time in seconds from being parked to setting temperature to 0. Use something like 86400 to wait 24h if you want to disable. Defaults to 600
lazy_home_when_parking: 1           # (default: 0 - disabled) - When set to 1, will home unhomed XY axes if needed and will not move any axis if already homed and parked. 2 Will also home Z if not homed.
shaper_freq_y: 103
shaper_freq_x: 33
shaper_type_y: zv
shaper_type_x: mzv


[tool 4]
tool_group: 0                     # Must be used and configured before this tool
extruder: extruder4
zone: 0,0,0
park: 0,0,0
offset:0,0,0
fan: partfan_t4
meltzonelength: 0 #18                 # Defaults to 0
idle_to_standby_time: 0.1          # Time in seconds from being parked to setting temperature to standby the temperature above. Use 0.1 to change imediatley to standby temperature. Defaults to 30
idle_to_powerdown_time: 1800       # Time in seconds from being parked to setting temperature to 0. Use something like 86400 to wait 24h if you want to disable. Defaults to 600
lazy_home_when_parking: 1           # (default: 0 - disabled) - When set to 1, will home unhomed XY axes if needed and will not move any axis if already homed and parked. 2 Will also home Z if not homed.
shaper_freq_y: 103
shaper_freq_x: 33
shaper_type_y: zv
shaper_type_x: mzv
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

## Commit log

2023-11-24 Initial Upload
    * Tool Locking Mechanism STL Files
    [Belt Clip Left.stl, Belt Clip Right.stl, MGN12 Carriage.stl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]
2023-11-24 Initial Commit
    * Tool Lock Carriage - CAD
    [Tool Lock Carriage.f3d]
2023-11-24 Tool Lock Assembly - Reorganised Initial Commit
    [Belt Clip Left.stl, Belt Clip Right.stl, MGN12 Carriage.stl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]
2023-11-30 Add files via upload
    Toolhead, Dock and Misc files
    [Dock - 2020 Mount.stl, Dock - Main Body.stl, Dock - Umbilical Mount.stl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]
2023-12-15 Alpha 2 Release
    Alpha 2 Release
    [mgn12-cut-guide.stl, tool-dock-spacer.stl]
2023-12-15 Superceded by Alpha 2 Files
    [EBB36 Mount.stl, Filament Sensor Encoder Mount.stl, Hotend Mount - Optical Trigger Flag.stl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]
2023-12-15 Superseded by Alpha 2 Files
    [Dock - 2020 Mount.stl, Dock - Main Body.stl, Dock - Umbilical Mount.stl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]
2023-12-15 Alpha 2 Release
    Alpha 2 Release of the DAKSH V2 Tool Changer
    [ab-motor-mount-left-1.stl, ab-motor-mount-left-2.stl, ab-motor-mount-left-3.stl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]
2023-12-15 re-exported due to error in original export
    [geared-servo-mount-front-left.stl, geared-servo-mount-front-right.stl]
2023-12-15 Rename geared-servo-mount-front-left.stl to geared-servo-mount-b x 2.stl
    [geared-servo-mount-b x 2.stl]
2023-12-15 Rename geared-servo-mount-a.stl to geared-servo-mount-a x 2.stl
    [geared-servo-mount-a x 2.stl]
2023-12-19 Create ToolLock Solid Assembly Alpha v2.step
    [ToolLock Solid Assembly Alpha v2.step]
2024-01-05 Fixed bugs
    Revised dock-mount.stl and dock-wireloom-extrusion-holder.stl
    [dock-mount.stl, dock-wireloom-extrusion-holder.stl]
2024-01-06 Fixed an issue with the first layer
    [ebb36-cover.stl]
2024-01-12 Tensioner Files missing
    [ab-motor-mount-tensioner-left.stl, ab-motor-mount-tensioner-right.stl]
2024-04-03 Add CAD STEP Files
2024-04-03 sample print images added
2024-04-07 Create Toolhead Extruder v49.step
    fixed holes misalignment
2024-04-07 Delete Toolhead Extruder v49.step
    Modded toolhead extruder to accomodate orbiter and sherpa mini. Sherpa mini will require printing of new dock.
2024-04-07 Create Daksh Extruder Mod v19.step
    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
2024-04-07 Create Toolhead Extruder v49.step
2024-04-08 CAD Files Updated
2024-04-08 Toolhead File Updated - Fixed Hole Alignment
2024-04-08 Added link to Complete Printer 3d Design File
2024-04-08 Create ExtruderMod
2024-04-08 Toolhead Extruder Mod
    Toolhead Extruder mod for the sherpa mini and orbiter
2024-04-08 Create Sherpa Mini-Orbiter-Extruder
2024-04-08 Extruder Mod
    Sherpa Mini and Orbiter toolhead mod
2024-04-14 Fixed
    Fixed dowel spacing for the acorn nut.
    Fixed separated spacer and motor mount to avoid support during printing
2024-06-21 Daksh Trident
    Latest cad for daksh trident
2025-01-29 Upload Complete Assembly for limepod's mods
